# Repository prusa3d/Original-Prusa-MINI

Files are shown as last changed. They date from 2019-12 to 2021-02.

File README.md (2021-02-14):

# Original Prusa MINI / MINI+

The Original Prusa MINI / MINI+ is a 3D printer project maintained by PRUSA RESEARCH. Originates in the RepRap project.

This repository contains resources and documentation for printed and mechanical parts of the printer.

**Links**

 * Prusa Research website : http://prusa3d.com
 * Product page: https://www.prusa3d.com/original-prusa-mini/
 * Build manual: https://help.prusa3d.com/en/tag/mini-2/

 * Buddy-board : https://github.com/prusa3d/Buddy-board-MINI-PCB
 * Heatbed : https://github.com/prusa3d/Heatbed-Mini-PCB
 * IR senzor : https://github.com/prusa3d/MKxS-IR-sensor

<p align="center">
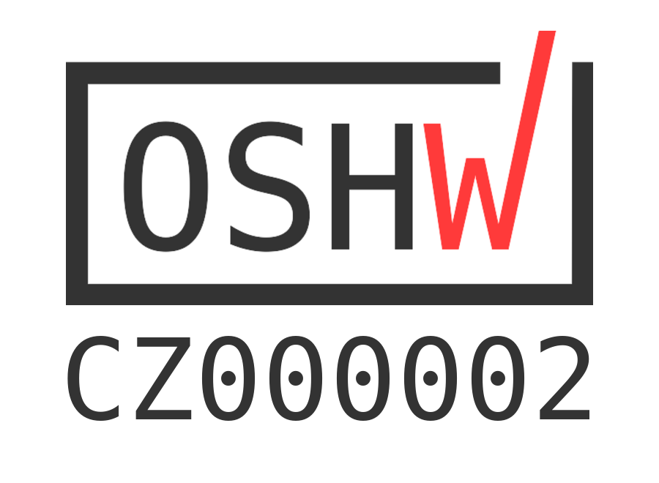
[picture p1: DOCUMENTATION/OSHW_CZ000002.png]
OSHW logo
  
</p>

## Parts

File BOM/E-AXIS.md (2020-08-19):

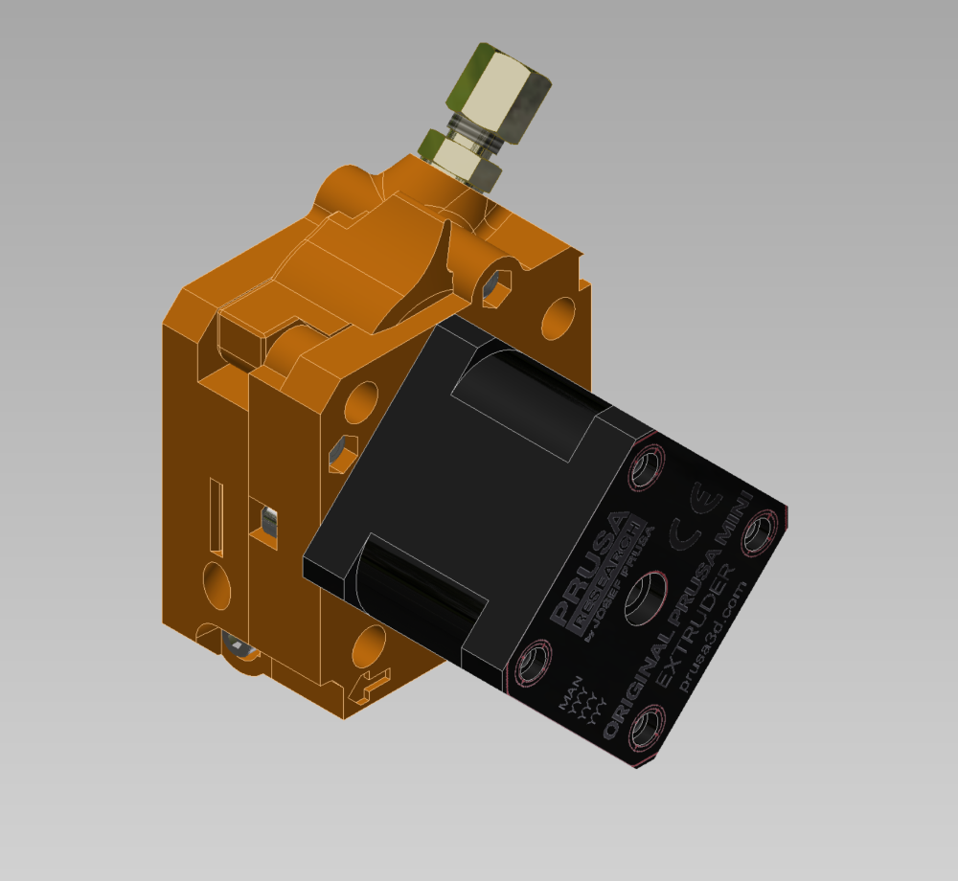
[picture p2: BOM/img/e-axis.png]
e-axis


**PRINTED PARTS**

|Name|Qty|
|:---|:---:|
|MINI-extruder-front|1|
|MINI-extruder-idler|1|
|MINI-extruder-rear|1|
|MINI-inspection-door|1|

**FASTENERS**

|Name|Qty|
|:---|:---:|
|M3x12 screw|3|
|M3x25 screw|6|
|M3x40 screw|1|
|M3n|4|
|M3nN|1|
|M3nS|1|

**ELECTRICAL PARTS**

|Name|Qty|
|:---|:---:|
|[MINI-E-axis motor](/DOCUMENTATION/ELECTRONICS/mini-motor-kit.pdf)|1|

**STANDARD PARTS**

|Name|Qty|
|:---|:---:|
|Bearing 625 2Z|2|
|MINI extruder idler spring|1|
|Zip tie|3|

**CUSTOM PARTS**

|Name|Qty|
|:---|:---:|
|[MINI fitting](/DOCUMENTATION/MECHANICAL%20PARTS/mini-fitting.pdf)|1|
|[MINI fitting swivel nut](/DOCUMENTATION/MECHANICAL%20PARTS/mini-fitting-swivel-nut.pdf)|1|
|[MINI fitting olive](/DOCUMENTATION/MECHANICAL%20PARTS/mini-fitting-olive.pdf)|1|
|[MINI motor pinion](/DOCUMENTATION/MECHANICAL%20PARTS/mini-motor-pinion.pdf)|1|
|[MINI filament spur](/DOCUMENTATION/MECHANICAL%20PARTS/mini-extruder-spur.pdf)|1|
|[MINI extruder PTFE tube 4x2x15](/DOCUMENTATION/MECHANICAL%20PARTS/PTFE-tube-extruder-15.pdf)|1|
|[MINI input PTFE tube 4x2x150](/DOCUMENTATION/MECHANICAL%20PARTS/PTFE-tube-input-150.pdf)|1|
|[MINI bowden 4x2x275](/DOCUMENTATION/MECHANICAL%20PARTS/PTFE-tube-bowden-275.pdf)|1|
|[MINI shaft 5x12](/DOCUMENTATION/MECHANICAL%20PARTS/mini-idler-shaft.pdf)|1|

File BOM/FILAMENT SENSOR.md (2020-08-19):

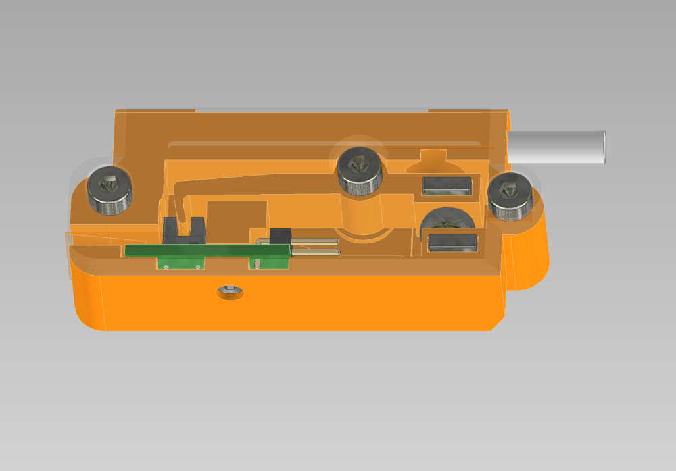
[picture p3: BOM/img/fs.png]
fs


**PRINTED PARTS**

|Name|Qty|
|:---|:---:|
|MINI-Fsensor-box|1|
|MINI-Fsensor-cover|1|
|MINI-Fsensor-lever|1|

**FASTENERS**

|Name|Qty|
|:---|:---:|
|M3x12 screw|4|
|M2x8 screw|1|

**ELECTRICAL PARTS**

|Name|Qty|
|:---|:---:|
|[IR filament sensor](https://github.com/prusa3d/MKxS-IR-sensor)|1|
|[IR filament sensor cable](/DOCUMENTATION/ELECTRONICS/mini-filament-sensor-cable.pdf)|1|

**STANDARD PARTS**

|Name|Qty|
|:---|:---:|
|Magnet 10x6x2|2|
|Stainless steel ball 7mm|1|

**CUSTOM PARTS**

|Name|Qty|
|:---|:---:|
|[MINI FS textile sleeve](/DOCUMENTATION/MECHANICAL%20PARTS/mini-oplet-5x300.pdf)|1|
|[MINI FS PTFE 4x2x15](/DOCUMENTATION/MECHANICAL%20PARTS/PTFE-tube-extruder-15.pdf)|1|

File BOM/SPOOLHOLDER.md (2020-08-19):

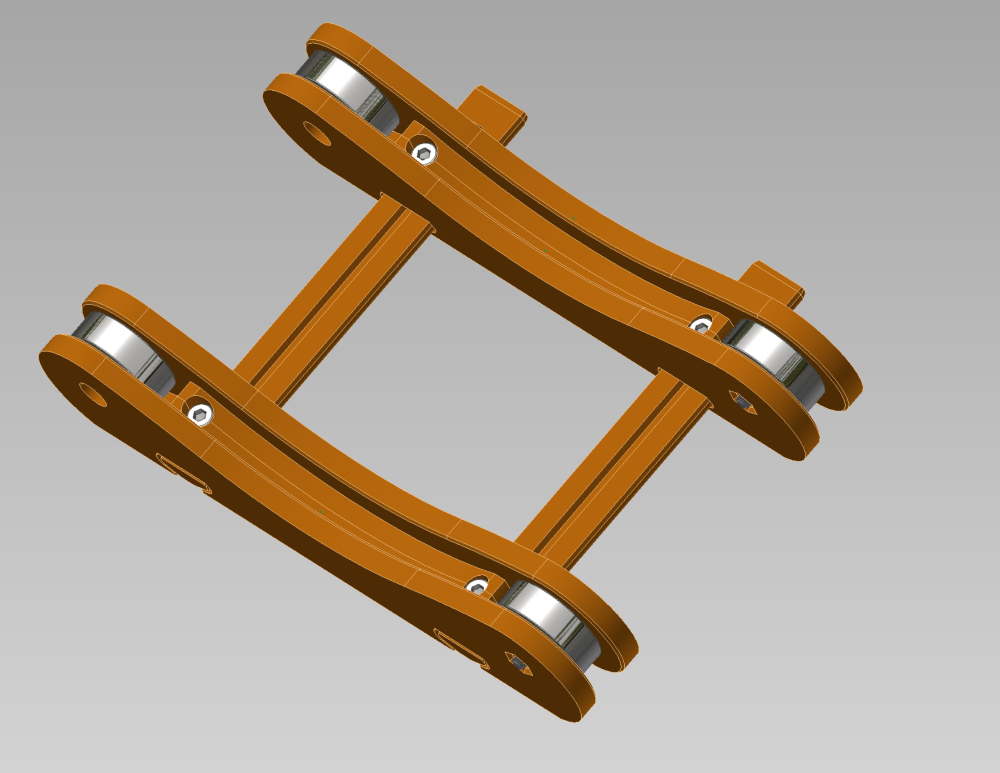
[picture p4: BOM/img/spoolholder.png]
spoolholder


**PRINTED PARTS**

|Name|Qty|
|:---|:---:|
|MINI-spoolholder-base|4|
|MINI-spoolholder-rail|2|

**FASTENERS**

|Name|Qty|
|:---|:---:|
|M3x8 screw|4|
|M3x12 screw|4|
|M3n|4|
		
**STANDARD PARTS**

|Name|Qty|
|:---|:---:|
|Bearing 608 2Z|4|

**CUSTOM PARTS**

|Name|Qty|
|:---|:---:|
|[MINI spoolholder foam pads](/DOCUMENTATION/MECHANICAL%20PARTS/mini-s-holder-pads.pdf)|4|

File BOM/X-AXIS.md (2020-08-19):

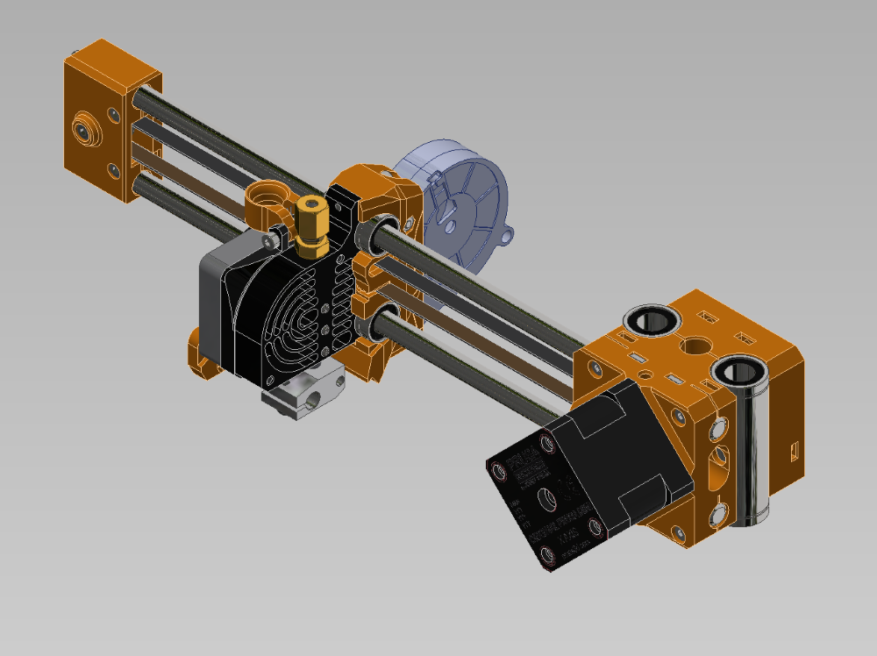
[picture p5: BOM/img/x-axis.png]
x-axis


**PRINTED PARTS**		

|Name|Qty|
|:---|:---:|
|MINI-x-carriage|1|
|MINI-x-end|1|
|MINI-z-carriage-front|1|
|MINI-z-carriage-rear|1|
|MINI-fan-spacer|1|
|MINI-fan-spacer-clip|1|
|MINI-minda-holder|1|

**FASTENERS**

|Name|Qty|
|:---|:---:|
|M3x12 screw|12|
|M3x20 screw|9|
|M3x30 screw|4|
|M3x10 button head screw|1|
|M3x4 grub screw|4|
|M3n|4|
|M3nN|1|
|M3nS|13|

**ELECTRICAL PARTS**

|Name|Qty|
|:---|:---:|
|[MINI hotend thermistor](/DOCUMENTATION/ELECTRONICS/mini-termistor.pdf)|1|
|[MINI heater](/DOCUMENTATION/ELECTRONICS/mini-heater.pdf)|1|
|[MINI heatsink fan](/DOCUMENTATION/ELECTRONICS/mini-extruder-fan.pdf)  ([DS](/DOCUMENTATION/ELECTRONICS/mini-extruder-fan-DS.pdf))|1|
|[MINI print fan](/DOCUMENTATION/ELECTRONICS/mini-turbine-fan.pdf)  ([DS](/DOCUMENTATION/ELECTRONICS/mini-turbine-fan-DS.pdf))|1|
|[MINI M.I.N.D.A.](/DOCUMENTATION/ELECTRONICS/mini-minda.pdf)|1|
|[2S connector](/DOCUMENTATION/ELECTRONICS/mini-2s.pdf)|1|
|[MINI X-axis motor](/DOCUMENTATION/ELECTRONICS/mini-motor-kit.pdf)|1|

**STANDARD PARTS**

|Name|Qty|
|:---|:---:|
|LM8UU linear bearing	|2|
|LM10LUU linear bearing|2|
|Pulley Bearing Idler 623h|1|
|Pulley Motor GT2-16|1|
|X-axis belt 561 mm|1|

**CUSTOM PARTS**

|Name|Qty|
|:---|:---:|
|[MINI X smooth rod](/DOCUMENTATION/MECHANICAL%20PARTS/mini-x-rod.pdf)|2|
|[MINI heatsink](/DOCUMENTATION/MECHANICAL%20PARTS/mini-heatsink.pdf)|1|
|[MINI heatbreak](/DOCUMENTATION/MECHANICAL%20PARTS/mini-heatbreak.pdf)|1|
|[MINI heaterblock](/DOCUMENTATION/MECHANICAL%20PARTS/mini-heaterblock.pdf)|1|
|[MINI nozzle 0.4](/DOCUMENTATION/MECHANICAL%20PARTS/mini-nozzle.pdf)|1|
|[MINI fitting](/DOCUMENTATION/MECHANICAL%20PARTS/mini-fitting.pdf)|1|
|[MINI fitting swivel nut](/DOCUMENTATION/MECHANICAL%20PARTS/mini-fitting-swivel-nut.pdf)|1|
|[MINI fitting olive](/DOCUMENTATION/MECHANICAL%20PARTS/mini-fitting-olive.pdf)|1|
|[MINI hotend PTFE tube 4x2x43.4](/DOCUMENTATION/MECHANICAL%20PARTS/PTFE-tube-hotend.pdf)|1|
|[MINI X motor textile sleeve](/DOCUMENTATION/MECHANICAL%20PARTS/mini-oplet-5x300.pdf)|1|
|[MINI hotend textile sleeve](/DOCUMENTATION/MECHANICAL%20PARTS/mini-oplet-8x700.pdf)|1|

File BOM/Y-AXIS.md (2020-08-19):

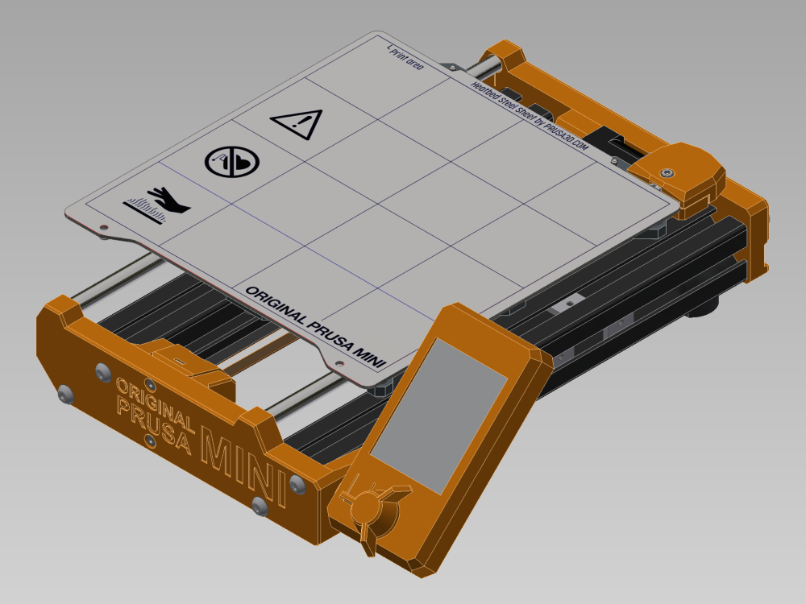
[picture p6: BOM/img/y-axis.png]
y-axis


**PRINTED PARTS**

|Name|Qty|
|:---|:---:|
|MINI-y-belt-holder|1|		
|MINI-y-idler|1|
|MINI-y-plate-front|1|	
|MINI-y-plate-rear|1|		
|MINI-heatbed-cable-cover-bottom|1|
|MINI-heatbed-cable-cover-top|1|		
|MINI-display-box|1|		
|MINI-knob|1|		

**FASTENERS**

|Name|Qty|
|:---|:---:|
|M3x8 screw|15|		
|M3x12 screw|7|		
|M3x20 screw|3|		
|M5x20r screw|8|		
|M3x4 Torx|9|		
|M3nN|11|		
|M3nS|2|		
|M3nE|3|		
|[M3x6 hex spacer](/DOCUMENTATION/MECHANICAL%20PARTS/mini-column.pdf)|9|		

**ELECTRICAL PARTS**

|Name|Qty|
|:---|:---:|
|[MINI heatbed](https://github.com/prusa3d/Heatbed-Mini-PCB)|1|		
|[MINI heatbed termistor](/DOCUMENTATION/ELECTRONICS/MK3s-HB-termistor.pdf)|1|		
|[MINI heatbed cable](/DOCUMENTATION/ELECTRONICS/mini-bed.pdf)|1|		
|[MINI Y-axis motor](/DOCUMENTATION/ELECTRONICS/mini-motor-kit.pdf)|1|		
|[MINI display](/DOCUMENTATION/ELECTRONICS/mini-display-ldopr28lcd-a003.zip)  [(driver DS)](/DOCUMENTATION/ELECTRONICS/mini-lcd-driver-st7789v.pdf)  [(lcd module DS)](/DOCUMENTATION/ELECTRONICS/mini-lcd-module-fw024tft-v14.pdf)|1|		
|[MINI lcd cable](/DOCUMENTATION/ELECTRONICS/mini-lcd-cable.pdf)|1|		

**STANDARD PARTS**

|Name|Qty|
|:---|:---:|
|LM8UU linear bearing|3|		
|Pulley Bearing Idler 623h|1|		
|Pulley Motor GT2-16|1|		
|Y-axis belt 496 mm|1|		 

**CUSTOM PARTS**

|Name|Qty|
|:---|:---:|
|[MINI aluminium extrusion 262mm](/DOCUMENTATION/MECHANICAL%20PARTS/mini-y-extrusion.pdf)|2|	
|[MINI Y smooth rod](/DOCUMENTATION/MECHANICAL%20PARTS/mini-y-rod.pdf)|2|		
|[MINI Y carriage](/DOCUMENTATION/MECHANICAL%20PARTS/mini-y-carriage.pdf)|1|		
|[MINI heatbed textile sleeve](/DOCUMENTATION/MECHANICAL%20PARTS/mini-oplet-5x350.pdf)|1|		
|[U bolt](/DOCUMENTATION/MECHANICAL%20PARTS/u-bolt.pdf)|3|		
|[MINI steel sheet](/DOCUMENTATION/MECHANICAL%20PARTS/mini-steelsheet-std.pdf)|1|		
|[MINI foam pad](/DOCUMENTATION/MECHANICAL%20PARTS/mini-foam-pad.pdf)|5|

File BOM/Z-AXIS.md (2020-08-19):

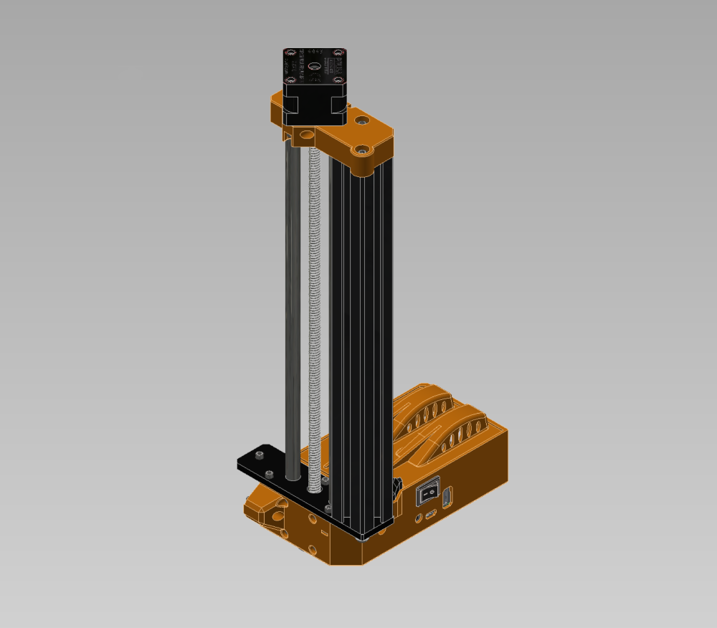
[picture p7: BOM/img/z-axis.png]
z-axis


**PRINTED PARTS**

|Name|Qty|
|:---|:---:|
|MINI-z-bottom|1|
|MINI-z-bottom-cover|1|
|MINI-z-bottom-cable-cover|1|
|MINI-z-top|1|

**FASTENERS**

|Name|Qty|
|:---|:---:|
|M3x8 screw|4|
|M3x12 screw|4|
|M3x20 screw|10|
|M3x40 screw|1|
|M5x16r screw|4|
|M3n|4|
|M3nS|10|

**ELECTRICAL PARTS**

|Name|Qty|
|:---|:---:|
|[MINI Buddy board v1.0.x](https://github.com/prusa3d/Buddy-board-MINI-PCB)|1|
|[MINI power switch](/DOCUMENTATION/ELECTRONICS/mini-power-switch.pdf)|1|
|[MINI display cable](/DOCUMENTATION/ELECTRONICS/mini-lcd-cable.pdf)|1|
|[MINI Z-axis motor](/DOCUMENTATION/ELECTRONICS/mini-motor-kit.pdf)|1|

**CUSTOM PARTS**		

|Name|Qty|
|:---|:---:|
|[MINI Z plate bottom](/DOCUMENTATION/MECHANICAL%20PARTS/mini-z-plate-bottom.pdf)|1|
|[MINI aluminium extrusion 289mm](/DOCUMENTATION/MECHANICAL%20PARTS/mini-z-extrusion.pdf)|1|
|[MINI Z smooth rod](/DOCUMENTATION/MECHANICAL%20PARTS/mini-z-rod.pdf)|2|

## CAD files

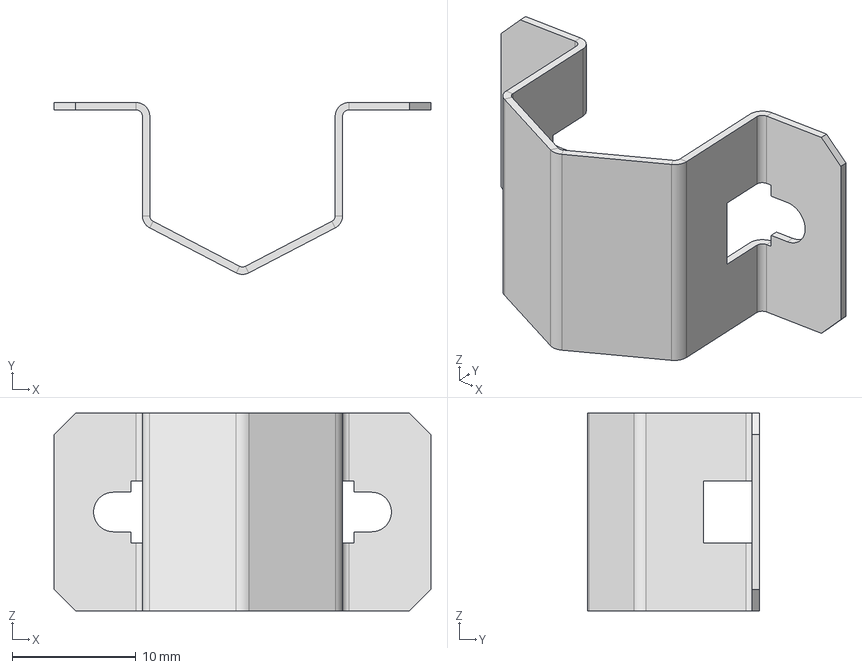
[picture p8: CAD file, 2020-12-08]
STEP/MECHANICAL PARTS/MINI-bearing-clip.stp
30.5 x 13.9 x 16.0 mm

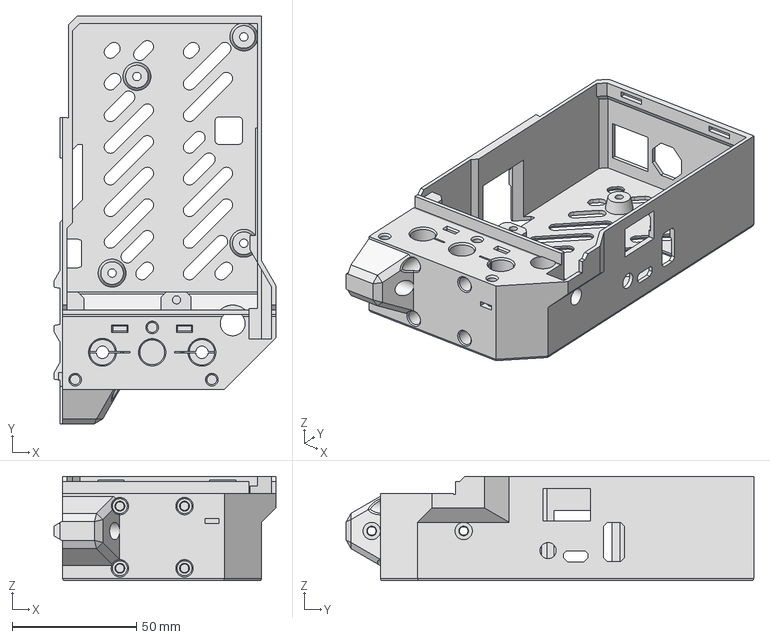
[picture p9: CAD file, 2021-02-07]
STEP/PRINTED PARTS/MINI-z-bottom.stp
89.3 x 163.9 x 42.0 mm

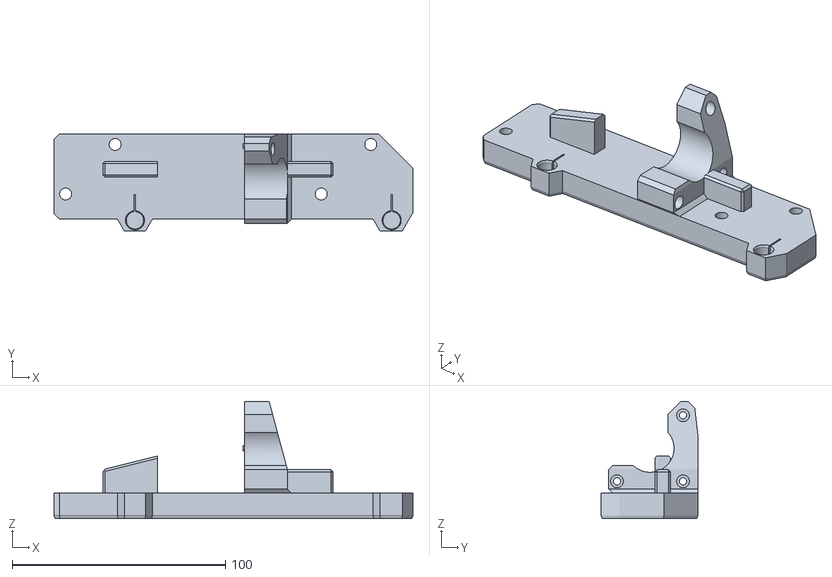
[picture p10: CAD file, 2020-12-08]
STL/MINI-y-plate-rear.stl
168.5 x 45.5 x 54.9

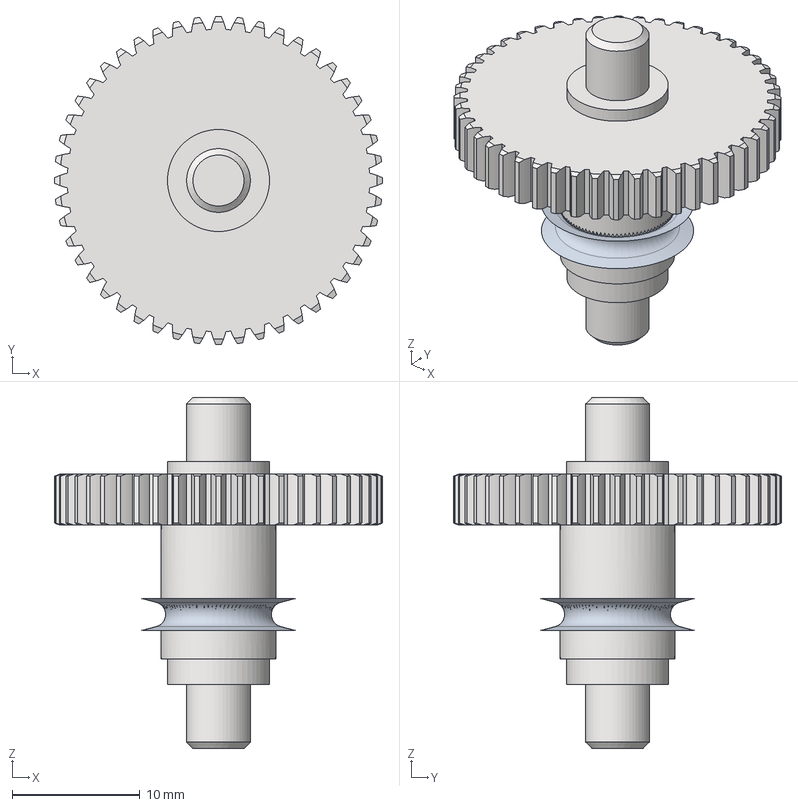
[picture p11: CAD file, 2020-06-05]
STEP/MECHANICAL PARTS/MINI-filament-spur.stp
25.7 x 25.7 x 27.5 mm

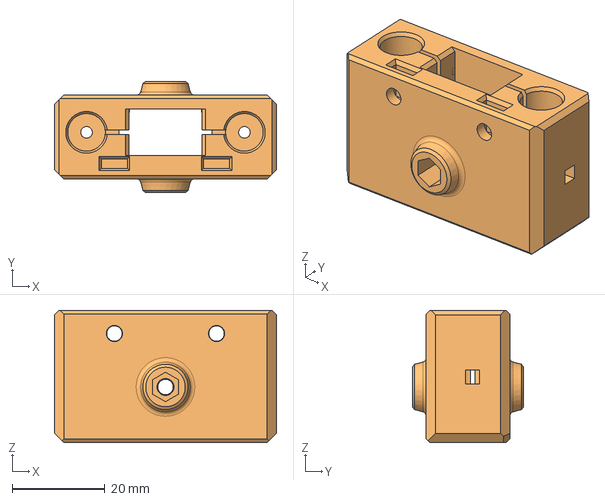
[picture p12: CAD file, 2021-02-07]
STEP/PRINTED PARTS/MINI-x-end.stp
47.8 x 24.0 x 28.5 mm

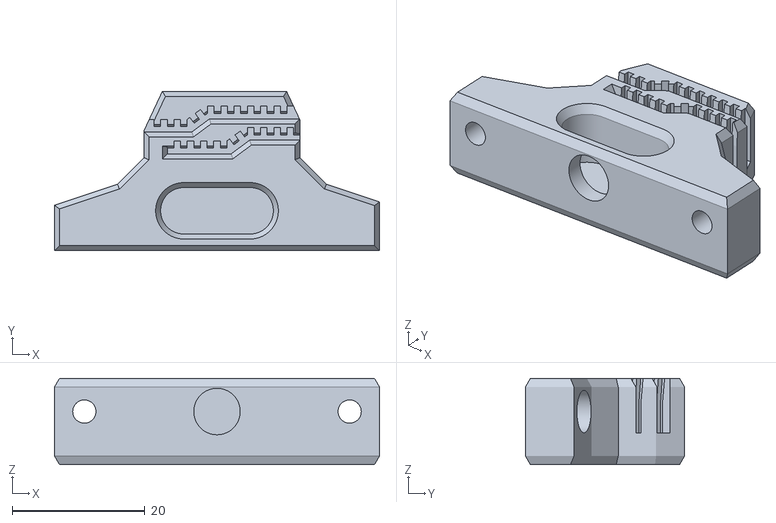
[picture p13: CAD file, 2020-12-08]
STL/MINI-y-belt-holder.stl
49.0 x 24.0 x 13.0

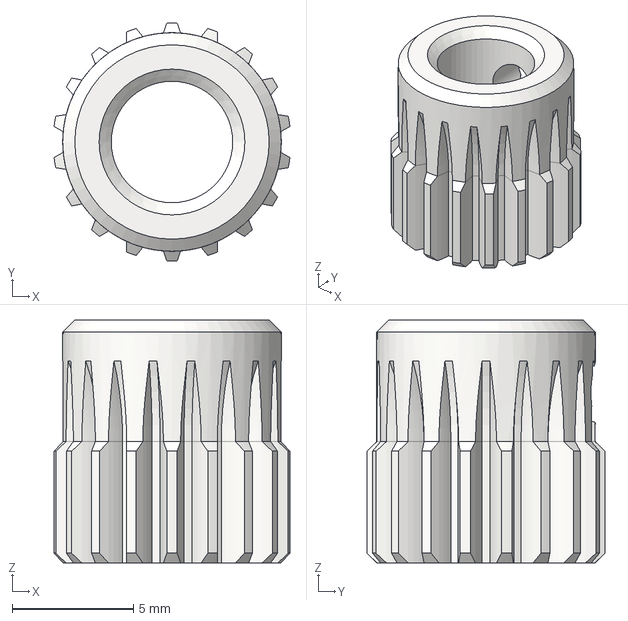
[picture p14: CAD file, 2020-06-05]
STEP/MECHANICAL PARTS/MINI-pinion.stp
9.72 x 9.80 x 10.0 mm

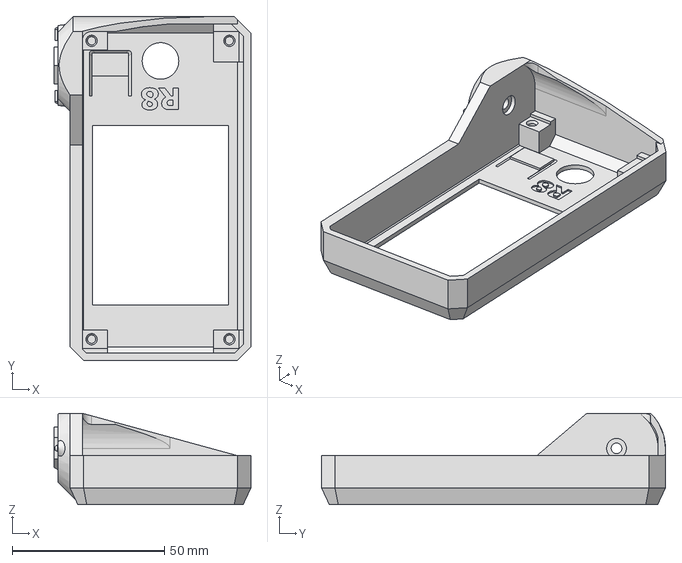
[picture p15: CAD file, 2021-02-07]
STEP/PRINTED PARTS/MINI-display-box.stp
64.6 x 112.9 x 30.0 mm

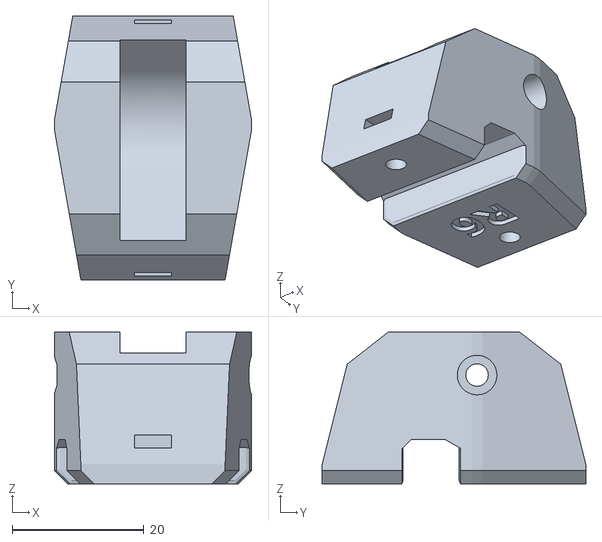
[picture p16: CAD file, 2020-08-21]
STL/MINI-y-idler.stl
29.9 x 40.0 x 23.0

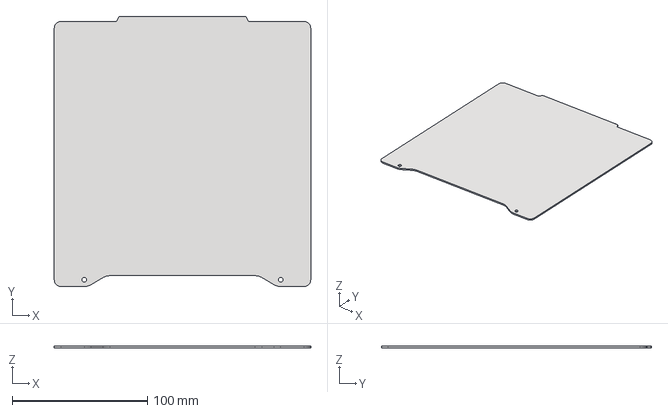
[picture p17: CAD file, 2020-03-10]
STEP/MECHANICAL PARTS/MINI-steel-sheet.stp
190.0 x 200.0 x 1.40 mm

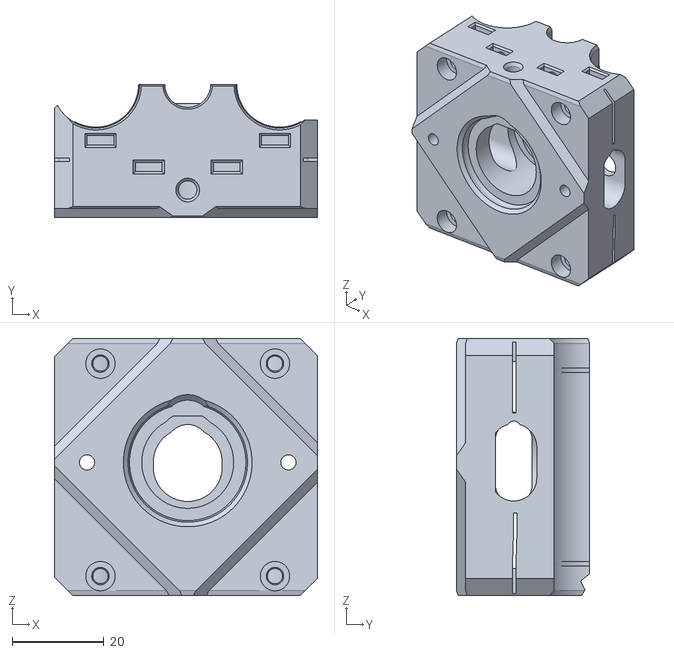
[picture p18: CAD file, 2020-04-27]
STL/MINI-z-carriage-front.stl
57.2 x 29.0 x 56.0

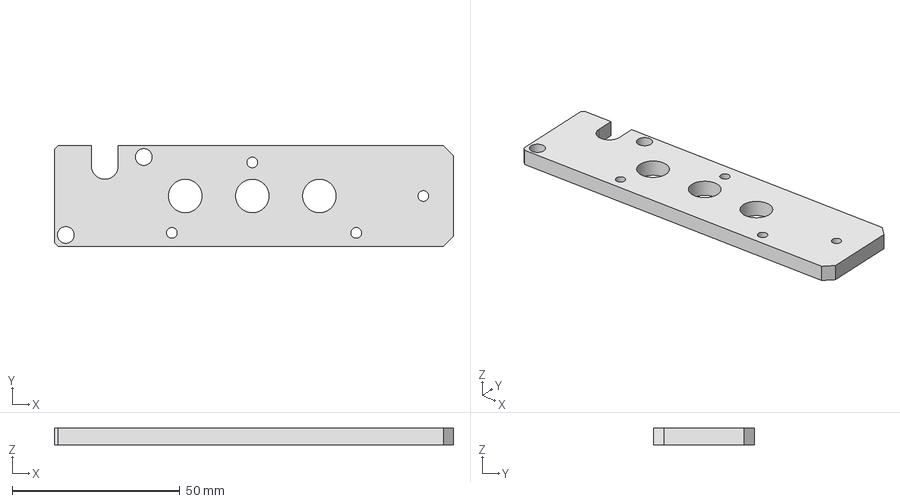
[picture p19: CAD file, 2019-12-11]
STEP/MECHANICAL PARTS/MINI-z-plate-bottom.stp
119.0 x 30.0 x 5.00 mm

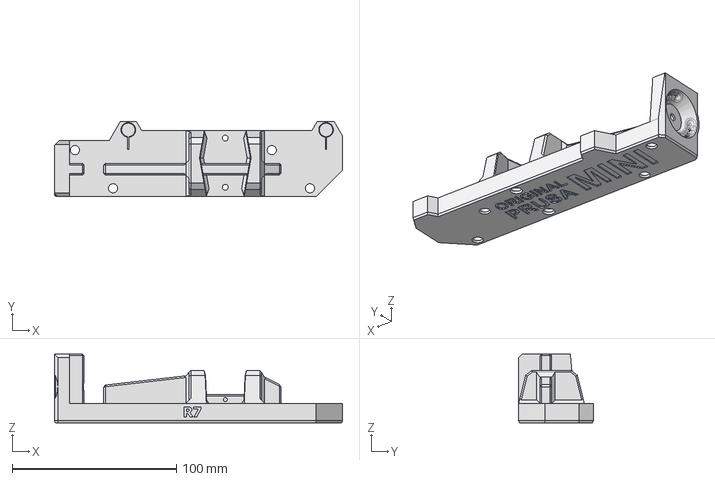
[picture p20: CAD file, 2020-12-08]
STEP/PRINTED PARTS/MINI-y-plate-front.stp
175.5 x 45.5 x 42.0 mm

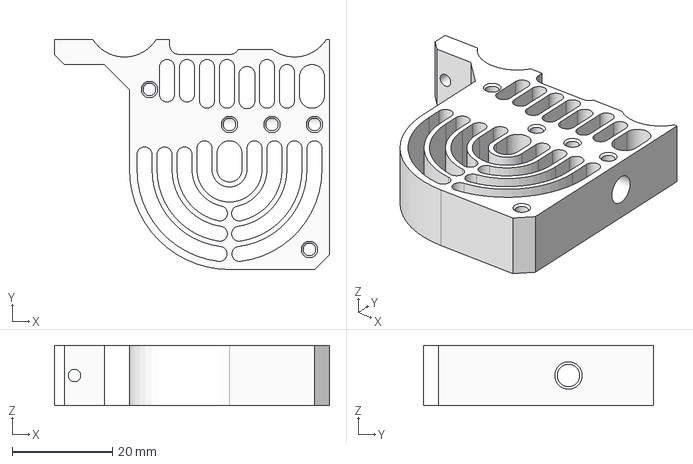
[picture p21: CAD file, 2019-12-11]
STEP/MECHANICAL PARTS/MINI-heatsink.stp
55.0 x 46.0 x 12.0 mm

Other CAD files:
STEP/PRINTED PARTS/MINI-y-plate-rear.stp
STL/MINI-z-bottom.stl
STEP/PRINTED PARTS/MINI-y-belt-holder.stp
STL/MINI-extruder-rear.stl
SOURCE/MECHANICAL PARTS/MINI-bearing-clip.ipt
SOURCE/MECHANICAL PARTS/MINI-filament-spur.ipt
SOURCE/MECHANICAL PARTS/MINI-heatbreak.ipt
SOURCE/MECHANICAL PARTS/MINI-heaterblock.ipt
SOURCE/MECHANICAL PARTS/MINI-heatsink.ipt
SOURCE/MECHANICAL PARTS/MINI-male-threaded-fitting.ipt
SOURCE/MECHANICAL PARTS/MINI-nozzle-0.4.ipt
SOURCE/MECHANICAL PARTS/MINI-olive.ipt
SOURCE/MECHANICAL PARTS/MINI-pinion.ipt
SOURCE/MECHANICAL PARTS/MINI-steel-sheet.ipt
SOURCE/MECHANICAL PARTS/MINI-swivel-nut.ipt
SOURCE/MECHANICAL PARTS/MINI-y-extrusion.ipt
SOURCE/MECHANICAL PARTS/MINI-z-extrusion.ipt
SOURCE/MECHANICAL PARTS/MINI-z-plate-bottom.ipt
SOURCE/PRINTED PARTS/MINI-base-spoolholder.ipt
SOURCE/PRINTED PARTS/MINI-display-box.ipt
SOURCE/PRINTED PARTS/MINI-extruder-front.ipt
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

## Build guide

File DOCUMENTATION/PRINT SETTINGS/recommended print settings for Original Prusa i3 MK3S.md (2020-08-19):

### Recommended print settings :

Printer : **Original Prusa i3 MK3S**

Print settings : **0.20mm Quality**

Material : **Prusament PETG**

Nozzle : **0.4 mm**

Layer : **0.2 mm**

Support : **no supports**

### **Edit :**

Infill pattern : **grid**

Infill density : **10 %**

<br/>

### **Parts :**

- MINI-z-bottom-cover

- MINI-z-bottom-cable-cover

- MINI-fan-spacer

- MINI-fan-spacer-clip

- MINI-fsenzor-box

- MINI-fsenzor-cover

- MINI-fsenzor-lever

- MINI-minda-holder

- MINI-inspection-door

- MINI-knob

- MINI-heatbed-cable-cover-bottom

- MINI-heatbed-cable-cover-top

- MINI-rail-spoolholder

- MINI-base-spoolholder

-------------------------------------------------------------------------------------------------------------------

### Recommended print settings :

Printer : **Original Prusa i3 MK3S**

Print settings : **0.20mm Quality**

Material : **Prusament PETG**

Nozzle : **0.4 mm**

Layer : **0.2 mm**

Support : **no supports**

### **Edit :**

Infill pattern : **grid**

Infill density : **20 %**

<br/>

### **Parts :**

- MINI-x-carriage

- MINI-x-end

- MINI-y-belt-holder

- MINI-y-idler

- MINI-y-plate-rear

- MINI-y-plate-front

- MINI-z-carriage-rear

- MINI-z-carriage-front

- MINI-z-bottom

- MINI-z-top

- MINI-extruder-rear

- MINI-extruder-front

- MINI-extruder-idler

- MINI-display-box

-----------------------------------------------------------------------------------------------

Please keep in mind thermal expansion of used material especially in XY plane. Printed parts are tempered by heatbed - then cooled down to room temperature so parts shrink.

```
Apply this linear relation: delta D´ = D * gamma * delta T
	delta D´	= final dimension difference
	D		= original dimension
	gamma		= coefficient of thermal expansion for used material
	delta T		= printed part temperature difference between current temperature 
			  while it's printed and ambient temperature in use

Example:
material	PETG: 	HB temp. = 90 [°C]
			amb. temp. = 25 [°C] 
delta T		90 - 25 = 65 [°C]
gamma		0.000068 [m/m*°C] [1/°C] (doesn't matter if Celsius or Kelvin)
D		100 [mm]
Use basic unit!

delta D´ = D * gamma * delta T
delta D´ = 0.1 * 0.000068 * 65
delta D´ = 0.000442 [m] = 0.442 [mm]
```

Linear thermal expansion works for each layer if there's any delta T but every layer has different delta T if the heatbed temperates printed part - the higher layer position the smaller delta T. It's due to cooling printed part by ambient air and air flow from print fan.

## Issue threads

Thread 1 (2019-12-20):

M600 / Filament change

Kasperc88, 2019-12-20:
There is two issues with the Original Prusa MINI and M600 (Filament change) that can be fixed with firmware.

Issues:

1#
When the printer unload the filament it will turn off the nozzle. This is fine. To load the new filament you have to press continue on the LCD,
and the printer will now heat up the nozzle to the target temperature. Once it hit the target temperature it will begin loading the filament.

This mean you have to sit and wait while you push the new filament into the tube so the printer can grab it. If it was not grabbet from the start
the filament will not be loaded correct and this lead to issue #2.

#2
After the printer thinks it have loaded the filament it will ask you if the color is correct. You can press "No" and it will extruder a small amount
of filament. But after this it will start to print. You do not get a new chance to say the color still isn't correct.

Fixes:
#1 - A option to tell the printer to begin loading the new filament
#2 - More chances to tell that the color isn't correct.

Bonus:
It could be helpfull if the z-axis raise alot more so we can clean the nozzle without burning our hands.

joeynuggetz, 2019-12-24:
Agree with the filament loading/unloading especially during a color change. Just got a ruined print because the filament didn't load on the first attempt (extruder gears didn't grab filament). Instead of asking if filament loaded just like any other printer it just assumed everything was fine when I said "no" to the color ok message. This needs to be fixed asap as color prints will fail if there are any problems encountered while loading new filament.

I do not have the filament sensor. Not sure if having one would have helped in this case.

charlesramsay, 2020-01-04:
I have found it impossible to unload PETG several times.  The unload routine does not allow the filament to be completely released.  I came up with a solution.  I cut the strand from the spool. Then I purge the remaining filament until it's beyond the stepper motor. Then I undo the bowden tube at the stepper. It works.

JohnnyDeer, 2020-06-15:
Hi @Kasperc88 , this issue is related to Prusa-Firmware-Buddy. Is duplicate of https://github.com/prusa3d/Prusa-Firmware-Buddy/issues/260 and https://github.com/prusa3d/Prusa-Firmware-Buddy/issues/361 so i´ll close this one. Thank you for suggestion and understanding.

Closed 2020-06-15.

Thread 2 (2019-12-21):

Not a firmware issue - MINDA height

AndyThirtover, 2019-12-21:
Dear Prusa

   My Mini was shipped with a lose MINDA.  It was not clear in the manual what the procedure for setting up the MINDA.  I got on to Tech Support and went with 1mm.

   So far my Mini does not have a perfect first layer for large prints - it is working though!

   I would like to be able to send jobs from my desk to the Mini which is in the basement.

   It would be useful to know progress of prints or be able to use OctoPrint.

   Overall, the finish is not quite as good as my 5000hr Mk3i3.

Regards

Andy

JohnnyDeer, 2020-06-15:
Hi @AndyThirtover , let me summarize your issue... first part with MINDA was solved with help of our Tech Support. Second part will be possible trough Prusa Connect in future. And you can use OctoPrint on MINI already.
First thing is about hardware and have been solved. Other suggestions are about firmware. So i´ll close this issue. You can crate feature request with your suggestion on Prusa-Firmware-Buddy. Thank you.

Closed 2020-06-15.

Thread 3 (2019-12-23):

STL and STEP Files don't open

6ffm70, 2019-12-23:
I'm having troubles opening the 3d files:
STL won't open in Prusaslicer; STEP won't open in two different professional CAD applications. I've also tried this on different computers to no avail.

Strankler, 2019-12-25:
same here.

6ffm70, 2019-12-30:
I've got this resolved:
I opened the downloaded files with an editor, and the first line showed the <html opening tag. Repeat for all tested files - positive.

I've downloaded the files with Chromium, using #RMB #Save link on the file link in the repo. Well, it's not the file that is linked, but another page.

Issue corrected by cloning the repo.

Closed 2019-12-30.

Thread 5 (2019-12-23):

Mesh Levelling has very weird behaviour

AndyThirtover, 2019-12-23:
4.0.1 Please view:

https://www.youtube.com/watch?v=rOWLI0K9chY

You'll see that the points 1-2 work perfectly and the 3-4-5 only go UP.  6-7-8 are ok and and that the MINDA does not operate.  Notice that 6-7-8 are ok and then 11-12 and 13 also go up (as do all of the points on the left hand side of the bed.

The net result is that this printer cannot be first layer calibrated.   It seems that the issue gets worse every time I power cycle/factory reset the printer.    I've managed one print on 4.0.0 but since the 4.0.1 upgrade this sad Prusa Mini has not managed a single print ;)

gregsaun, 2020-01-07:
@michalxfanta I suspect this is due to the too short cables on the hotend which wear the cables quicker than expected. I have made an improvement on your parts to help, you can find it here: https://www.thingiverse.com/thing:4065410

Is Prusa working on a solution for this issue? The best way I see today would be to provide a longer heater cartridge cable because this is the shortest and most problematic one.

JohnnyDeer, 2020-06-16:
Hi, this behavior is because cables of MINDA are broken. We sended replacements with new MINDA type and improved cable holder, wich solving this problems. If you still have this kind of MINDA issue please contact our Tech Support. Thank you.

Closed 2020-06-16.

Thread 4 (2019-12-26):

MINDA cable wire break (mesh bed leveling unexpected behaviour/does not proceed)

6ffm70, 2019-12-26:
**Description**: 4x4 point mesh bed leveling does not finish as expected. When process starts, MINDA light is off;
probing pos. 1 - the print head moves _up_ (couple of mm)
probing pos. 2 - the print head moves _up_ (couple of mm)
probing pos. 3 - MINDA light switches on, print head moves _down_, then up; here the process halts.

When moving the X-axis, the MINA light switches on in a position further away from the extruder; and switches off approximately at the same position when moving back into direction of the extruder.

This behaviour is reproduceable. With every go, the Z-Axis moves further up by a couple of mm.

**Analysis**: with the printer switched on, the MINDA light on or off, moving the MINA cable by hand makes the MINDA light flicker.

**Assumption**: at least one of the conductors in the MINDA cable is broken after ~30 hours of operation.

6ffm70, 2019-12-29:
**More Analysis**: locating the wire break in the cable
1. MINDA and cable in situ: removed textile sleeve, singled out MINDA cable
2. marking (I) the position of the top cable tie on the cable for reference (28.5cm from MINDA):
3. bending the cable starting at the sensor, moving in direction of connector end while watching the MINDA light
4. marking (II) the first position where the light flickers first (24cm from MINDA)
5. switching off printer, removing connector and cable
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
6. clean cutting cable on marking II in direction of MINDA
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
7. removing outer cable 15mm and wire isolation 7mm from cut of connector section half
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
8. measuring each resistance of all three wires while bending the cable in different sections: black OK, brown OK, blue NOK
9. locating the approximate point of non-contact in the blue wire by watching the multimeter and bending the cable, starting from the connector; marking (III) the approximate point (39cm from MINDA)
10. carefully stripping blue wire isolation from cut into direction of marking III
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
11. noting down position where stranded wire is separated (**29cm** (IV), **33.5cm** (V) from MINDA)
12. checking the remainder cable length for breaks with resistance measurement

6ffm70, 2019-12-29:
### There is no evidence for the root cause of the wire break so far. As long as the root cause is not eliminated, any replacement of the MINDA ass'y or repair hack is a temporary solution.

**Repair hack**:
Parts required: 5x cable ties 2.5mm, 4x wire end sleeves*, heat shrink hose ø3mm, ø6mm as required
Tools required: wire stripper 4mm², 0.25-0.4mm², copper wire shear, end sleeve crimp pliers (open type) 0.5mm²*
*alternatively a heat controlled soldering iron and soldering wire

1. clean cut off section with broken wire strands
2. stripping shortened blue wire for 7mm
3. preparing new isolated (yellow in pictures) wire in length of broken/removed wire with 7mm isolation stripped of both ends
4. crimping (to avoid uncontrolled heat) end of blue wire with one end of new wire with an end sleeve
5. isolating wire junction with heat shrink hose
6. removing outer cable 15mm and wire isolation 7mm from cut of MINDA section half
7. preparing 3x heat shrink hose over wire end, and 1x heat cable sleeve replacement shrink hose over cable in length of stripped section +30mm
8. repeat crimp connection for 3x wire connection
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
9. isolate 3x wire junction with heat shrink hoses
10. heat shrink cable sleeve replacement hose
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
11. place MINDA assembly back in printer using new cable ties
12. hope that changed internal wire resistances don't affect sensor operation

gregsaun, 2020-01-07:
The hotend cables on the Prusa Mini are very short and stressed which could potentially have damaged your wire quicker than expected.

I made a fix for those too short cables in case you want to solve it:
https://www.thingiverse.com/thing:4065410

6ffm70, 2020-01-14:
More follow up:

1. The cable as repaired above made the printer go again; however Mesh Bed Leveling gave different results by +/-0.400 each time, resulting in unsuccessful prints.
2. Replacing the repaired MINDA assembly with a new one provided by P/R support resolved this issue.
3. The cause of 1.) is unknown to me. Assumptions: one or both of the wires not repaired were damaged, and this was not detected during multimeter tests; or the repair affected sensor operation.

JohnnyDeer, 2020-06-16:
Hi @6ffm70 , we sended replacements with new MINDA type and improved cable holder, wich solving this problems. If you still have this kind of MINDA issue please contact our Tech Support. Thank you.

6ffm70, 2020-08-01:
Hello @JohnnyDeer, can you please elaborate on what is meant with _new MINDA type_? I've had a couple of MINDAs replaced by tech support, and they all showed similar symptoms, even with the improved cable holder.

6ffm70, 2020-08-26:
Follow up: new MINDA details added here: https://github.com/prusa3d/Original-Prusa-MINI/blob/master/DOCUMENTATION/ELECTRONICS/mini-minda.pdf

Closed 2020-06-16.

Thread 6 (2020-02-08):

MINI-y-plate-front.stl

VapeN3D, 2020-02-08:
Not able to download

JohnnyDeer, 2020-06-16:
Hi @VapeN3D , if you have issues with downloading on github, you can download file with all SLTs on our page ... https://www.prusa3d.com/prusa-i3-printable-parts/ . Same for your issue #17 . I´ll close both issues.

Closed 2020-06-16.

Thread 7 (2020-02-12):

Create high contrast large text size screen mode for people with limited vision

mrjohnc, 2020-02-12:
Create high contrast large text size screen mode for people with limited vision

This would include research on how to create accessibility modes for the screen by looking at guidelines and talking to groups of people with limited vision.

This mode may also include making additional sounds on certain actions to keep the user informed to what the printer is doing.

JohnnyDeer, 2020-06-15:
Hi @mrjohnc ,  this FR is related to firmware. Please create new one on Prusa-Firmware-Buddy following issue templates. I´ll close this one. Thank you for understanding.

Closed 2020-06-15.

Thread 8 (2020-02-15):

WiFi module support

rjkrause, 2020-02-15:
I have a question about the WiFi module.  In ESP 01 is the default FW or some modified version?  Or in the current version of FW in Buddy Board is still not supported WiFi ?

3d-gussner, 2020-04-06:
@rjkrause This question should be asked in https://github.com/prusa3d/Prusa-Firmware-Buddy.

Please close the issue.

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

JohnnyDeer, 2020-06-15:
Hi @rjkrause , this issue is related to firmware and is duplicate. I´ll close this one.

Closed 2020-06-15.

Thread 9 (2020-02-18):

Clicking Extruder gears

Superkirky, 2020-02-18:
Perhaps consider using helical gears for the extruder mechanism, to minimise backlash/noise. At the moment this is the most annoying/noisy part of the printer. Or perhaps stay with spur gear but include at spring loaded tensioning of the gear to reduce backlash/noise.

JohnnyDeer, 2020-06-22:
Hi @Superkirky , we know about this problematics, thank you for suggestion.

SnickCH, 2021-12-26:
How about using a dual gar extruder? maybe one like the extruder from the i3? Then you have a tested design that works

https://github.com/prusa3d/Original-Prusa-MINI/issues/58

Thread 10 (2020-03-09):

File names should scroll

hurley78, 2020-03-09:
File names should scroll because PrusaSlicer makes long file names and it makes it difficult to pick the file you want to print.  You can't see the filament type or print time.  Should scroll like MK3S.

3d-gussner, 2020-03-09:
@hurley78 This is a firmware issue you should post in https://github.com/prusa3d/Prusa-Firmware-Buddy

3d-gussner, 2020-04-06:
@hurley78 Can you please close the issue here?
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

Closed 2020-04-06.

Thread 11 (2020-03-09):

Stopping a print causes the printhead to crash into printed part.

HenrikPankoke, 2020-03-09:
I had a print with 6 elements printing individual.
The elements is place like the photo. print is from back left to back right.
moving to front left to front right
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

When printing the front right element I stopped the print.
the printhead then moves backwards an into the element behind. causing this to be knocked of the plate. In this case it was a small part and not theat high adhesion. But larger parts with could adhesion could have damage that fan on the printhead.
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

maybe changing stop command to move the nozzle up above highest printed element, before moving in any other direction. or just move nozzle clear of current print and stop movement.

HenrikPankoke, 2020-03-09:
Sorry. created this the wrong place. Don't know how to delete.
Moved to https://github.com/prusa3d/Prusa-Firmware-Buddy/issues/257

3d-gussner, 2020-04-06:
@HenrikPankoke you find a `Close issue` button below ;-)
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

JohnnyDeer, 2020-06-15:
I´m closing this issue as duplicate.

Closed 2020-06-15.

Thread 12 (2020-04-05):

feature request: support multiple steel sheets like the MK3

iandouglas, 2020-04-05:
Would be awesome if the Mini's firmware allowed us to switch more easily between the smooth PEI and the textured PEI like the MK3 firmware.

3d-gussner, 2020-04-06:
Hi @iandouglas,

you posted the issue in the wrong repository. Please close it here and open it in https://github.com/prusa3d/Prusa-Firmware-Buddy

iandouglas, 2020-04-07:
thanks again @3d-gussner

Closed 2020-04-07.

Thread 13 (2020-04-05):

feature request: holding in the knob to raise/lower Z like the MK3

iandouglas, 2020-04-05:
I miss being able to hold in the knob and adjusting the Z height when the printer is otherwise idle. Could this be added as a firmware feature in the future?

3d-gussner, 2020-04-06:
Hi @iandouglas,

you posted the issue in the wrong repository. Please close it here and open it in https://github.com/prusa3d/Prusa-Firmware-Buddy

iandouglas, 2020-04-07:
thanks @3d-gussner

3d-gussner, 2020-04-07:
@iandouglas You are welcome

Closed 2020-04-07.

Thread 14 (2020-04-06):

problem with ethernet mac adress

klimma1508, 2020-04-06:
Hello, I wanted to connect the 3D printer Prusa MINI via cable to the Internet, but the mac address of the 3d printer has only 11 characters, even if it has 12 characters. Does Prusa MINI support the internet or is it a mistake? Thank you Klimš
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

bobc, 2020-04-10:
There is a zero missing, i.e. use "0a" instead of "a" : 109C 700A FEFF

But you should really submit an issue in the Buddy firmware repo.

JohnnyDeer, 2020-06-15:
Hi @klimma1508 , this issue is related to firmware and have been already solved in version 4.0.5. I´ll close this issue.

Closed 2020-06-15.

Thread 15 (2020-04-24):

Prusa Mini Factory USB Stick failing

feutl, 2020-04-24:
Hello,

after some people do report the same problem on the Prusa Forum, I thought I should let you know.
The USB Stick shipped with the Prusa Mini fails after some time being mounted. I was happy the firmware update went through, but every print on the USB stick failed.

Copied the files to another USB stick and everything worked straight away.

https://forum.prusaprinters.org/forum/hardware-firmware-and-software-help/factory-usb-drive-wont-stay-mounted-on-printer-crashes-failed-prints/
https://forum.prusaprinters.org/forum/assembly-and-first-prints-troubleshooting/watchdog-reset-2/

3d-gussner, 2020-04-24:
Hi, I think you posted in wrong repository.

feutl, 2020-04-30:
>
>
> Hi, I think you posted in wrong repository.

which one would be the right repo ?
I experienced this with the Prusa MINI - and the forum seems not the right place at all

abosson, 2020-05-21:
I had the same problem with the USB stick... Dôme " watchdog reset" I change the USB stick and copy thé file without reslicing and I have no problem tête!

JohnnyDeer, 2020-06-15:
Hi @feutl , this issue is related to firmware and is duplicate of https://github.com/prusa3d/Prusa-Firmware-Buddy/issues/255 . I´ll close this one.

Closed 2020-06-15.

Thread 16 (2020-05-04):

Entering and exiting menu

geoper2, 2020-05-04:
When jumping from a submenu back to the main menu, for example from Filament back to Main, the highlight goes back to the first item which is Print.
The same happens when editing values inside a submenu. Upon exit the highlight goes to the first item on the submenu. This is furstrating because you need to scroll through all of the menu items to get back to the item you were before.

It would be better for the user experience to keep the highlight in the same place that you were before exit or back. When exiting or going back the highlight needs to remain in the same item and not move to the first item on the screen.

3d-gussner, 2020-05-04:
@geoper2 As you have a firmware issue post this here: https://github.com/prusa3d/Prusa-Firmware-Buddy
Please don't to forget to close this one.

Closed 2020-05-04.

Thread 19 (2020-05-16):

Solution to relieve stress on the hotend cables

martin8425, 2020-05-16:
In reference of: https://www.prusaprinters.org/prints/16515-prusa-mini-minda-saver-cable-guide

This is not my solution, but have been using it for some time. Merging this idea onto MINI-extruder-front.stl seams like a no-brainer to me ;)

JohnnyDeer, 2020-06-15:
Hi @martin8425 , thank you for your suggestion, we take note of this possibility.

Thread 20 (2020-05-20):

ABS as Filament Option missing

feutl, 2020-05-20:
The problem got raised in the forum
https://forum.prusaprinters.org/forum/hardware-firmware-and-software-help/abs-profile-on-mini

There is no "setting" for ABS as a filament to change, load or unload within the Prusa Mini firmware. This is a little confusing and the temperatures which should be used for ASA and ABS also seem to be different as I have understood.

Can this profile can be added somehow to the firmware?

Thanks

feutl, 2020-05-25:
https://github.com/prusa3d/Prusa-Firmware-Buddy/issues/493 posted it at the buddy-board repo

Closed 2020-05-25.

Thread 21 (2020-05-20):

OpenSCAD?

infosisio, 2020-05-20:
Is there a particular reason that this wasn't designed in OpenSCAD as per the usual tradition?

Thanks.

JohnnyDeer, 2020-06-15:
Hi @infosisio , reason why we are no longer using OpenSCAD is that we found better solution.

infosisio, 2020-06-15:
@JohnnyDeer I don't know what solution you found but you are no longer sharing them in a format the community can build upon.

JohnnyDeer, 2020-06-22:
@infosisio we are still sharing all data in format which is usable to build upon.

infosisio, 2020-06-22:
@JohnnyDeer That is not true, STEP is an archival format that doesn't give parametric control. The only thing it is useful for is to act as reference for reverse engineering a part, in order to be able to make changes and improvements. Please reconsider this.

SyberxSpace, 2020-06-22:
From the headers in the released STEP files it appears they were generated using Autodesk Inventor. Example from MINI-x-end.stp:
```
FILE_NAME(
/* name */
'MINI-x-end.stp',
/* time_stamp */ '2020-01-22T16:21:13+01:00',
/* author */ ('Robert Turinsky'),
/* organization */ (''),
/* preprocessor_version */ 'ST-DEVELOPER v17.2',
/* originating_system */ 'Autodesk Inventor 2019',
/* authorisation */ '');
```
I believe this would mean that the STEP files are indeed not the source files, and that this would make the printer not open-source as claimed. This also severely hampers the speed and accuracy of community improvements. Even if you Prusa Research believes that STEP files are source files **(please make clear if this is the case)**, I think it can be agreed that the practice is against the community accepted definition of the term and how it is used to imply an ecosystem encouraging communal improvement and iteration.

CacikeOtoao, 2020-06-22:
Sadly this has been happening more often that a lot of us would like. They have been dragging their feet to release source files or just setting their own timelines and borderline redefining the licenses used to release their products. They have actually made changes to some of the “Open Source” products and not update the git files until been pressed on. @JohnnyDeer  it is not about releasing “usable files to build upon”, it is about releasing the actual source files for products that are touted as Open Source and come with a big Open Source logo stamped on the box.

infosisio, 2020-06-24:
@JohnnyDeer I am sorry to say this but we are not talking to a wall here. You've heard our points clearly and you owe us a response. You market something as open source when it's not. Please explain yourselves.

CacikeOtoao, 2020-06-24:
I will also like an explanation, hopefully this is not a case of #openwashing.

lord-carlos, 2020-06-24:
It's a bit like releasing a binary Java file and calling it open source because you can decompile it.

It's nice that Prusa is releasing the step file, but calling it an open source printer at the same time is appalling.
On the shop site it even says:
> All parts of our printer are open-source.

infosisio, 2020-06-26:
@CacikeOtoao Unfortunately so far this seems to be the case...

josefprusa, 2020-06-30:
Let me clarify and correct some statements here from our side.
We have used openSCAD for long time, but from certain moment we needed to switch to more advanced sw for several reasons - starting from increasing speed of development, documentation, more advanced features available and ending up with easier exchange of data with our suppliers.
For GIT we choose STEP file format as this is widely used for exchange of data ( STEP = Standard for the Exchange of Product model data) and in fact it has been requested often by developers who did not like openSCAD in MK3 repository as alternative. Also, STEP files are widely accepted by various CAD software, it is standard how to exchange CAD information but   I do agree that STEP is not ideal for later development as you do loose some functionality or information as discussed here.
Starting with MINI repository we will add native source files in addition to STEP files ( we now use Autodesk Inventor ) and missing pieces of documentation in short time.

infosisio, 2020-06-30:
@josefprusa Thank you for agreeing to provide the source files but allow me to say as a response to your argument that STEP is not sufficient for an open source project, it is simply not the source file. Thanks.

SyberxSpace, 2020-07-01:
Thank you @josefprusa for agreeing that native source files are important for the community to develop and improve in an open and efficient manner. I'm hoping this will also carry over to the mk3s parts that also lack source files at the moment.

In the future you might want to consider a different license on release and make it clear what your release schedule and intents are from the beginning. "Surprises" like the appendix being released post-preorder and the lack of files and firmware tools aren't good for the community or how your brand is seen by the community. Not too long ago you were an outstanding example of what was good in the open community and these recent evens have begun to tarnish that. I don't think it's too late to turn that around though!

TLDR: The community is smart enough to understand if you just tell them what you plan outright. Just be **open** about it and stay faithful to the true intent of the open-source practice if you really want to be called open-source. Don't just do the minimum to keep the open tag on your products as it just makes you look untrustworthy.

I'm excited and hopeful for the future!

ucirello, 2021-02-23:
Prusa can keep the Autodesk Inventor files - as long as they release a version in openscad (or freecad for that matter) that the community can open and modify at source level, not at archive level (like Step or STL).

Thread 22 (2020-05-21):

Scrolling name of print for mini ?

abosson, 2020-05-21:
hello, I would suggest you  an improvement for the Mini !

the name of the print file is fixed and sometimes when you have to print the same part but with a différent material , the type of material is at the end of the name !

unfortunely, we can see it like on the MK3.

if it could be "scrolling" it could be great.

I don't if it's possible with the new mainboard but it would be useful in my case (when you have the listing)

JohnnyDeer, 2020-06-15:
Hi @abosson , this issue is related to Prusa-Firmware-Buddy and is duplicate of https://github.com/prusa3d/Prusa-Firmware-Buddy/issues/249 . I´ll close this one. Thank you for suggestion and understanding.

Closed 2020-06-15.

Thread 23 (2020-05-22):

Feature request: Loading filament improvement.

nigeljohnson73, 2020-05-22:
When you're loading, that step where it says click next to load, then gives you exactly zero seconds to ram filament in... well, it could turn the extruder stepper slowly to get the filament a catch, then clicking next would perform the load. That would be sooooo helpful.

JohnnyDeer, 2020-06-15:
Hi @nigeljohnson73 , this is also related to firmware and is similar to https://github.com/prusa3d/Prusa-Firmware-Buddy/issues/260 . I'll close this one.

Closed 2020-06-15.

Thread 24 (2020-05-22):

Feature request: loading filament - don't heat the bed

nigeljohnson73, 2020-05-22:
It's not required for the loading process, and it's wasteful.

JohnnyDeer, 2020-06-15:
Hi @nigeljohnson73 , this FR is related to firmware. Please create new one on Prusa-Firmware-Buddy following issue templates. I´ll close this one. Thank you for understanding.

Closed 2020-06-15.

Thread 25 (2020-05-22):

Feature request: loading filament - cooldown after load

nigeljohnson73, 2020-05-22:
You have to select a filament regardless of the current nozzle temp so it will heat up (even from cold), but you should also automatically cool down after the load as well... or remove the option to heat so that people know they have to to do it and stop the heating before walking away leaving the hot-end hot.

JohnnyDeer, 2020-06-15:
Hi @nigeljohnson73 , this issue is related to firmware and is duplicate of https://github.com/prusa3d/Prusa-Firmware-Buddy/issues/439 and https://github.com/prusa3d/Prusa-Firmware-Buddy/issues/221 . I'll close this one.

Closed 2020-06-15.

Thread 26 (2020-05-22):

Feature request: loading filament - use current temps

nigeljohnson73, 2020-05-22:
What if my particular filament isn't on the list??? allow for using the current temp, or remove the list... how is that list updated?

JohnnyDeer, 2020-06-15:
Hi @nigeljohnson73 , this FR is related to firmware. Please create new one on Prusa-Firmware-Buddy following issue templates. I´ll close this one. Thank you for understanding.

Closed 2020-06-15.

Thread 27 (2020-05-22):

Feature request: Show last M117 message

nigeljohnson73, 2020-05-22:
Yeah there is an option to look at all the messages, but it would be nice to see the last one on the screen somewhere just so you can watch the status as you run through your printer start code for example.

JohnnyDeer, 2020-06-15:
Hi @nigeljohnson73 , this FR is related to firmware. Please create new one on Prusa-Firmware-Buddy following issue templates. I´ll close this one. Thank you for understanding.

Closed 2020-06-15.

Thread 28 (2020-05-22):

Feature request: access the menus system while "Remote Printing"

nigeljohnson73, 2020-05-22:
I love the OctoPrint logo when it's connected, but you cannot access the menus so, for example, you cannot load filament. You need to power cycle the printer do the load, then go back to octoprint to reconnect.

JohnnyDeer, 2020-06-15:
Hi @nigeljohnson73 , this issue is related to firmware and is duplicate of https://github.com/prusa3d/Prusa-Firmware-Buddy/issues/360. I'll close this one.

Closed 2020-06-15.

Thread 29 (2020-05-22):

Bug: Disconnecting "Remote Printer" does not return control to the Mini

nigeljohnson73, 2020-05-22:
When you connect OctoPrint, you get the big logo. But, when you disconnect OctoPrint, the printer does not detect this and so you are forced to power cycle the printer to get control back. A workaround would be #28

Gordontgopher, 2020-06-06:
You've opened a number of issues in the hardware repository. The developers are more likely if you raiser them in the firmware repository (https://github.com/prusa3d/Prusa-Firmware-Buddy)

JohnnyDeer, 2020-06-15:
Hi @nigeljohnson73 , same as #28. I´m closing as duplicate.

Closed 2020-06-15.

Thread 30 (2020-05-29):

Spool holder

okaerin, 2020-05-29:
I want to print additional spool holder for my prusa mini. To do so I would need the required parts. Unfortunately I havent seen a part list. Is there one?

EuphoricPenguin, 2020-07-01:
https://trello.com/b/IHnQ677R/part-list-bom

pltaylor, 2021-05-27:
I know this is almost a year old, but I think this could be closed out now that the BOM is located here https://github.com/prusa3d/Original-Prusa-MINI/blob/master/BOM/SPOOLHOLDER.md

Closed 2021-05-27.

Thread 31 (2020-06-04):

Extruder Gears STEP files missing.

CacikeOtoao, 2020-06-04:
Hi,
The extruder for the MINI seems to be under the same license as the other components but the STEP files are not included. Is the extruder not Open Source? Any reason for the delay of the files been release?

akukan, 2020-06-05:
Missing parts have been uploaded, sorry for delay.

Closed 2020-06-05.

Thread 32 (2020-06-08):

Magnet Improvement Suggestion

Porch11, 2020-06-08:
I use the Prusa Mini almost daily. The steel plate installation and removal could be made easier if the magnets didn't pull it from a range/distance. I would suggest replacing them with Polymagnets; which are programmed permanent magnets that can be made from any magnet grade.

I believe they will give a better user experience, hold the plate better and be cheaper than the current system as it requires 12 magnets. I think with Polymagnets, you could get away easily with 8.

Here is a link to attachment Polymagnets: https://catalog.polymagnet.com/polymagnet-products/attach.html

JohnnyDeer, 2020-06-15:
Hi @Porch11 , thank you for your suggestion, we take note of this possibility.

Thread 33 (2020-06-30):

Multicolor print - unsuccessful load filament

Wolfram3D, 2020-06-30:
When print of first color is done there is color changing phase. When load of new filament/color is successful everything is ok but when load is not successful (eg extruder doesn't grab the filament) there is no chance to repeat load filament - just question if color is ok.

Is possible to improve it like:
1) print of first color
2) color change phase ->
   a) auto unload filament -> was filament successfully unloaded? When "Y" then press continue to load new filament. When "N" then repeat this step "unload filament".
   b) load filament -> was filament successfully loaded? When "Y" then purge and question if color is ok.... When "N" then repeat this step "filament loading".

Thanks

JohnnyDeer, 2020-07-07:
Hi @Wolfram3D , you are in bad section. Your issue is related to Buddy firmware and this issue is solved in FW version 4.1.0-RC1, i'm closing this one.

Closed 2020-07-07.

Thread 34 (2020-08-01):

Prusa Mini Open Source Design

6ffm70, 2020-08-01:
Seeing the good attitude towards open source hardware, software and mechanic design at Prusa Research marks a new era for me. An innovative, fast growing company that benefits from sharing, and lets others benefit from sharing:
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
Looking at the mechanic design in the repositories here, I have the impression that the open source design promise is not met, when I compare this to the creation of software: everything is available to modify, build and test it to a highly productive level.
External people, individuals and professional contribute, and have the opportunity to try new features.

Not so on the mechanic side - this is pretty much closed to Prusa internal and largely undocumented and incomplete. If traces are to be found, they are scattered over different sites in different categories. This is a missed opportunity to let P/R and the community benefit from open-source.

6ffm70, 2020-08-01:
To have this set up, I'd like to see

- 3d design definitions that can be modified. Unlike #21 , I don't think that has to be a particular file format like openSCAD. Inventor and STEP files should be okay, as people used different CAD systems to contribute. Though, if external references or skeleton models are used, this should stay intact within the native CAD files.
- Product and component specifications: the requirements for the entire product should be broken down to component level - including engineering drawings or model based definitions. Test cases and criteria, tolerances, tolerance calculations, and where applicable D-FMEA.
- If there are third party components that are not open source, they should include a datasheet and a customer volume model; if those parts are customer (Prusa) directed, like some E3D components on the Mk3, the specifications and all other open source data should be included too.
- Production data - the saying goes that Prusa printers can reproduce large parts of themselves (for all 3d-printed components), yet, there's only STL files in the repo, and no printing parameters. I'm with #18 here - why keep the -no doubt- super refined and experienced printing parameters P/R internal? The 3mf files, and the material properties should be open too.
- Everything in one place: an example: I only learned by chance that Mk3 and Mk3s use different PTFE tube diameters by tenths of a millimetre. That information was buried deep in support articles; even though it's relevant to function of the printer, and I was troubleshooting mine. I see that Github is more limited to version 3d designs while maintaining file relations, than a PDM system. Maybe enhance prusaprinters.org to host community design projects, and showcase this function by maintaining all engineering data for the printers there?
When this is properly set up, I'm sure external designer will branch out designs, test, enhance, etc. The current quality of sharing is discouraging this, to be honest.

gregsaun, 2020-08-01:
I think you made a good summary of the situation.

However, I am not okay with STEP file being a source. Even for designing a simple cube you have to start with a sketch and some defined dimensions and constraints (90° angle for example). If you export as STEP you loose this sketch and so part of the logic behind the design. Note that the dimensions and constraints are not the only logic you are loosing but also the sequence used to design a part. Some parts can be fairly complex to design and requires some special steps.

Just a side note regarding MK3(S) printers, they have never been sold as open source as far as I remember. Nothing was ever mentioned in this sense on the prusa3d.com pages nor in the launch video. It was just made well enough to think it is an open source printer but it is not. The Prusa Mini is different as it has been claimed in several places to be an open source printer and they even mention "All parts of our printer are open-source" (and not _all printed parts_).

6ffm70, 2020-08-01:
@gregsaun, this is grabbed from https://www.prusa3d.com/about-us/ , and this is what I also mean by good attitude towards open source hardware - it covers everything:
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
The fragments of the i3 Mk3/s design published in the github repo have the GPL licenece attached as well as the MINI.

I don't think the _sources_ of the mechanic design are deliberately incomplete. **Lack of an established method to collaborate in public may be a cause for this.**

This is also where STEP (subject to a lot of discussions eg. here https://github.com/prusa3d/Original-Prusa-i3/issues/139, https://github.com/prusa3d/Original-Prusa-i3/issues/84#) comes in as an _addition_ to the native format - it opens up editing access to the highest possible share of the community.

The tool of choice for the main branch will be set by the main developer; yesterday it was openSCAD, today it's Inventor (or some that identifies as Inventor), tomorrow it's another solution that fits the development requirements.

I think your concerns about the STEP format are valid; while at the same time my issue is the completeness of the _source_ of all mechanical engineering aspects of the printers.

Example: even if all native parametric 3d files were published online, you'd still only see how they were drawn/modelled, but not how the whole system works, or which design features or tolerances/materials have been chosen to overcome e.g. a heat dissipation challenge. You'd not be able to build on this knowledge to enhance this feature.

When calling the whole product, thus also the mechanical engineering _open source_, the community should be able to engineer the whole printer from scratch to make the project benefit from its contributions.

gregsaun, 2020-08-02:
@6ffm70 I agree for the STEP file, it is important to me to share them if you want to share properly your project. However they are not the source. You can create a STEP from the source but can't create the source from the STEP file. GPL is clear, you must share the source, it is not optional.

I agree with you that a CAD files alone isn't valid, you need to have the drawings for the tolerances/material/surface finish for "metal" parts and the print settings for the printed parts.

Good point regarding the about-us section. Then a lot more is missing like the specs of the fans, the specs of the extruder spring, the magnet specs, the whole BOM, etc. And this is valid for MK2(S) and MK2.5(S) as well (and probably MK1).

_> I don't think the sources of the mechanic design are deliberately incomplete. Lack of an established method for open collaboration may be a cause for this._
I think the community here starts to see this differently now. It is really not the first time we ask for the source files for MK2(S), MK2.5(S), MK3(S) and MINI. They had many many chances to fix this.

EuphoricPenguin, 2020-08-25:
I think the recent additions might push this thread closer to being closed, but there's still a distinct lack of community involvement on the hardware side; at least we have more or less complete documentation.

6ffm70, 2020-08-26:
@EuphoricPenguin , I agree, this is a leap forward!
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
JohnnyDeer, 2020-11-19:
Original Prusa MINI is now certified by Open Source HW Aliance - https://certification.oshwa.org/cz000002.html
I believe this issue can be closed as well as #21, @6ffm70 ?

lord-carlos, 2020-12-08:
> Original Prusa MINI is now certified by Open Source HW Aliance - https://certification.oshwa.org/cz000002.html
> I believe this issue can be closed as well as #21, @6ffm70 ?

That is only for software, no?
Hardware is "other"

ucirello, 2021-02-23:
By effectively forcing the use of a closed source software for the original design, this printer should not be labeled as open source hardware. Especially, because Autodesk Inventor is a very expensive software. By using an expensive proprietary software, Prusa is effectively locking contributions and fork out of this design.

6ffm70, 2021-03-02:
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

That's true - there is no licence for the hardware; and no licence for the documentation; just links to the github repo.
@JohnnyDeer can you please be more specific as to what has been certified?

bomarspub, 2021-03-17:
I found this to me an interesting read. I am currently reviewing the mechanicals, and several things are puzzling. I get it that its a volunteer effort, but maybe a little mechanical drafting guidance is in order. One thing is the absence of a preferred vendor part number is absent from the drawing.  Two  The mechanical call outs seem to be all over the map and need more explanation to the intention. Possibly a legend for international sharing to make more sense out of them. Cases where bubbles indicate there should be a second sheet or a defined note, yet absent. Just using the rods as a simple example, X rod is missing the rockwell spec.  Certainly can purchase this over the counter , but it would be nice to have a preferred vendor to work with. my two cents..

pltaylor, 2021-05-27:
> By effectively forcing the use of a closed source software for the original design, this printer should not be labeled as open source hardware. Especially, because Autodesk Inventor is a very expensive software. By using an expensive proprietary software, Prusa is effectively locking contributions and fork out of this design.

It may not be in the true spirit of open source, but asking Prusa to hamstring themselves by forcing the use of open source design tools may be a bridge too far.  At the end of the day Prusa is a business and they need to use the tools they think will help them get the job done.  Every step towards a pure open source is commendable, but like everything else in engineering there has to be a balance of multiple factors.

ucirello, 2021-05-27:
@pltaylor they can keep the originals in a closed format, and release the source in a open format that actually has the same object tree (freeCAD comes to mind, but not only). No need to hamstring themselves - but take the effort of saving into more (and open) formats.

pltaylor, 2021-05-27:
But if you submit a PR they would have to then do a manual merge into their preferred design software.  If the goal is to make modifications for yourself, then yes, your suggestion works.  But if the goal is to actually collaborate and grow the platform then your suggestion doesn't scale much better than the current state of things.

ucirello, 2021-05-27:
So just declare Mini to not be open source and be done with it.

6ffm70, 2021-05-29:
> But if you submit a PR they would have to then do a manual merge into their preferred design software. If the goal is to make modifications for yourself, then yes, your suggestion works. But if the goal is to actually collaborate and grow the platform then your suggestion doesn't scale much better than the current state of things.

I can see your point, and I believe it is a description of the ideal situation - which should certainly be the goal.
At the same time, the software available for collaborative mechanical design (PDM and CAD) is excellent for productivity and maintaining references, file associations and design intents; however none of these is open source.

This leaves the STEP format as the lowest common (open) exchange format, for the price of abandoning design parameters and intent, but maintaining accuracy. For now, the best every creator of opensource design data can do, is publishing STEP and native formats and what is available from the aforementioned (https://github.com/prusa3d/Original-Prusa-MINI/issues/34#issuecomment-680780459) documentation.

There is clearly a gap in tools for online open collaboration in mechanical design as compared to software development, and Prusa obviously does not take advantage of merge requests for mechanical design in this and the other github parts repositories; though increasing the amount of data in this MINI repo has been a step in the right direction.

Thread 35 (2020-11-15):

Extruder rear piece.

SgtKiLLx, 2020-11-15:
So, I need to do a new extruder rear piece for my Mini.. and.. the bigger hole that the brass fitting piece twists into, with larger spaced threads , I attempted to get it screwed in, and the whole thing split.

JohnnyDeer, 2020-11-18:
Hi @SgtKiLLx please contact our Support with this case. Chat in right down corner https://shop.prusa3d.com/en/ thank you.

SgtKiLLx, 2020-11-18:
> Hi @SgtKiLLx please contact our Support with this case. Chat in right down corner https://shop.prusa3d.com/en/ thank you.

Prusa chat support doesn't know shit. I don't see how they can help with this. There is no way that this piece was heated up and threaded in.

Closed 2020-11-18.

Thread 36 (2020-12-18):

Automatic skew correction.

riodoro1, 2020-12-18:
Are there any plans to bring skew correction to the MINI?
Ive noticed my printer is quite out of square (XY and YZ) and it’s not an uncommon problem on the internet.
Are the circles on the heat bed PCB actually there for this purpose and this would just need to be implemented in the code?

JohnnyDeer, 2021-01-19:
Hi @riodoro1, this issue should be in Prusa-Firmware-Buddy repository and is related to https://github.com/prusa3d/Prusa-Firmware-Buddy/issues/385. I´m closing this one.

Closed 2021-01-19.

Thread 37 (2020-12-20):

Bed heating up when unloading filament

hemdrup, 2020-12-20:
Why does the bed heat up when unloading filament? (This is not when printing, but directly from the home menu)

Prusa Mini+ , version 4.2.1

 https://youtu.be/dRz50qD_JEE

JohnnyDeer, 2021-01-13:
Hi @hemdrup, this issue should be in Prusa-Firmware-Buddy repository and its duplicate of https://github.com/prusa3d/Prusa-Firmware-Buddy/issues/706
I´m closing this issue.

Closed 2021-01-13.

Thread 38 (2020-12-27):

Request pre heating 5-10sec to prevent failsafe in cold climates

boobslappy, 2020-12-27:
I am requesting adding a 5-10 preheat to raise thermistors above threshold for those of us with our printing in cold areas. I’m having to use a blow dryer and don’t see why it couldn’t heat for a bit before checking thermistors. Could this feature be added? I’m on a prusa mini+. Thanks.

TickTock-, 2020-12-31:
Yes.  Please!  (or lower the threshold)

JohnnyDeer, 2021-01-13:
Hi @boobslappy this requirement should be in Prusa-Firmware-Buddy repository, please open it there according to the templates.  I´m closing this one here.

Closed 2021-01-13.

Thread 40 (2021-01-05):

Filament run out sensor failing to pause print

M8Harry, 2021-01-05:
Had a print run out of filament but the mini kept printing.

The sensor has done this once in the past (older firmware version) but it has saved a print as well on the previous version.

Sucks seeing 4hrs of a 9hr print wasted because the printer didn't stop. When loading new flament I tested the sensor when it detected filament the filament the menu on screen updated and i pulled it out it changed back. So the sensor is working when not printing but it's hit and miss during prints.
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

JohnnyDeer, 2021-01-18:
Hi @M8Harry, with this issue please contact our Tech Support (chat is on right side down ... https://shop.prusa3d.com/en/ ).

Closed 2021-01-18.

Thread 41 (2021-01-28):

Extruder Idler Arm Broke

Rockohaulic, 2021-01-28:
My Recommendation:
Update part per my design.  Extend length of arm slightly and have a thru-hole for the nut.  Place the nut all the way on the back side of the arm.
Then the plastic part would be under compression instead of tension!   No more failed parts!   :-)

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

JohnnyDeer, 2021-02-23:
Hi @Rockohaulic, thanks for your suggestion, we showed it to our developers.

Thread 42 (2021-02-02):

why can not connect mini to pronterface

Surealjedeye, 2021-02-02:
I have been trying to figure this out. I have easily connected 4 other branded printers to pronterface via usb. I connect the mini to my computer through usb. The computer recognizes it on Com 7. No matter the baudrate selected pronterface can not connect. I have tried everything me and my son can figure out. I just ended a chat with Prusa customer support and I was referred to this forum. Please help. I am so frustrated at the moment.

BogdanH59, 2021-05-25:
On Windows 10 I can connect Pronterface to MINI (I use baudrate 250000). Did you use mini USB port on MINI?

DRracer, 2021-07-30:
@Surealjedeye is your issue still relevant? Have you tried the latest FW 4.3.2-RC2?

zoltanbaranyai, 2022-12-15:
I have the same issue, any solution? Latest FW on printer and installed the latest driver from the prusa site.

Prusa-Support, 2023-01-03:
Hello. As mentioned in the Handbook, the micro USB port allows further third-party applications and custom uses.

> The micro USB port can be used to run third-party solutions

https://cdn.prusa3d.com/downloads/manual/prusa3d_manual_mini_en.pdf

This means that as of now, the use of it is not directly supported by Prusa Research. In fact, I'm afraid our drivers pack doesn't include any specific drivers for the correct functionality of the Prusa MINI via computer.
A user suggested some specific drivers in the Forum. Feel free to test this suggestion or take part in the discussion.
https://forum.prusa3d.com/forum/general-software-discussion/mini-and-pronterface-not-connecting/#post-489157

Other than this, apparently, there are two types of micro-USB cables on the market: charge/power-only cables and data/sync cables. The difference is apparently the power transmission capacity and the number of threads inside. You may want to make sure to use a cable suitable for data transfer.

Michele Moramarco
Prusa Research

DRracer, 2023-01-04:
Standard serial line is available on the MINI without limitations, but:
- baudrate needs to be set to 115200 bd
- you really need to use a data/sync micro-USB cable
- I'd recommend using firmware 4.4.0 and/or 4.4.1-RC1. There have been some issues with the serial line in the beta releases before 4.4.0

FYI: opening the serial line at 57600 bd shall be used for debugging - it makes the MINI send Marlin logs. This way you cannot issue G-codes into the printer.

The best way of checking whether the MINI connects to a computer is to look into the operating system logs and search for something like:
```
kernel: usb 1-1.2: New USB device found, idVendor=2c99, idProduct=000c, bcdDevice= 2.00
kernel: usb 1-1.2: New USB device strings: Mfr=1, Product=2, SerialNumber=3
kernel: usb 1-1.2: Product: Original Prusa MINI
kernel: usb 1-1.2: Manufacturer: Prusa Research (prusa3d.com)
kernel: usb 1-1.2: SerialNumber: CZPX.............
kernel: cdc_acm 1-1.2:1.0: ttyACM5: USB ACM device
```
This confirms, that Linux "sees" the new serial device - the MINI. From now on the serial port `/dev/ttyACM5` can be used to talk to the printer.

SimonTratter123, 2023-01-07:
I am able to use Octoprint with an Raspberry Pi with the micro USB port on the Mini. However I can't connect the mini to my computer to use Pronterface. Devicemanager does not find any device refering to the mini.

Prusa-Support, 2023-01-19:
Unfortunately the drivers are not included.
Please try the drivers suggested by the community on the forum.
Also make sure the micro USB port is not damaged in any way (wobbly, enlarged, detached or dry soldering...).

Michele Moramarco
Prusa Research

hkienle, 2025-02-12:
> micro USB port

Just to emphasize, because this may be easily missed: The USB-A port will not work, you have to connect to the USB Micro port that sits to the left of the USB-A port.

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
Source: https://help.prusa3d.com/article/octoprint-configuration-and-install_2182

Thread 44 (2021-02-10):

STOP button during Purge/Load/Unload

re490, 2021-02-10:
On my MINI+ (firmware 4.3.0 and prior) there is a STOP button displayed at the bottom of the screen during Purge/Load/Unload operations but it can't be selected.  It would be convenient to be able to stop these operations.

JohnnyDeer, 2021-02-11:
Hi @re490, this issue should be in Buddy FW repository and is duplicate of https://github.com/prusa3d/Prusa-Firmware-Buddy/issues/370 . I´m closing this one, thank you for understanding.

Closed 2021-02-11.

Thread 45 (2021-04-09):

USB stick occasionally becomes unreadable.

damiandixon, 2021-04-09:
Firmware: 4.3.1+2759

USB stick (one supplied with printer) is ejected correctly from Windows but occasionally becomes unreadable on insertion into printer and subsequently still unreadable on re-insertion into windows laptop.

Happened twice now. Both times reformatted.

raymate, 2021-04-09:
Try another stick, may not be the firmware. A few users have reported the supplied stick becomes bad or not work well. I didn't even bother using it. I got myself a Kingston branded one. DTSE9, I have two versions one 32GB and an older 4GB. The 4GB work without any issues. The 32GB sometimes does not show up in the printer. This is what he latest firmware might fix as its USB driver related. Most say use a stick no bigger than 8GB. I tend to agree with current stable firmware. But getting hold of small USB sticks is becoming hard, I looked and I would need to resort to eBay to get a 4GB stick now days. So I hope once this latest firmware becomes live it will let me use my 32GB stick with no issue.

damiandixon, 2021-04-21:
A new 4GB USB integral drive seems to be working fine.

Closed 2021-04-21.

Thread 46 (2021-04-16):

Change Filament confirmation

Freland, 2021-04-16:
When changing speed it it quite easy to press "Change Filament" in the menu. Which is quite annoying. An easy confirmation "Yes/No" would solve this "issue" easily.

JohnnyDeer, 2021-05-18:
Hi @Freland, you are in wrong repository this is FW related and it´s duplicate of https://github.com/prusa3d/Prusa-Firmware-Buddy/issues/1387. I´m closing this issue.

Closed 2021-05-18.

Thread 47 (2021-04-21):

Problems with Hostnames in firmware 4.3.1 (Using more than one Prusa mini)

waltercwitt, 2021-04-21:
Repost from prusa printers forum
"
Hello,

I've been chasing this issue around for quite some time now, but it appears that no-one else is having a similar issue. At work, I've setup 2 Prusa MINIs with both of them connected to our network via the same ethernet switch. I set them up with the hostnames, http://prusamini1 and http://prusamini2 to make it easier for people to remember where to check the status of there prints.

The problem I'm having is, sometimes after restarting the printer, the hostname gets wiped, and the printers can only be accessed by there IP address, and in rare cases, one of the printers will take the hostname of the other. This was actually happening a bit before firmware 4.3.0, but it seems to have gotten far worse after updating them.

During my troubleshooting of the issue, I discovered some very odd things that the printers where doing:

- If, during power on, there was a flash drive that had a lansettings.ini file on it plugged into the machine, It would overwrite it's current settings with the ones in the file. (I'm pretty sure this is what was causing one printer to take the others hostname)
- When I save the LAN settings to a flash drive, the hostname it saves is always blank, even when the hostname is set and working. (I am not allowed to set as static IP for the printers at work, so I can't verify if any of the other settings are returning default values as well.)
- When I load the LAN settings from a flash drive using the menu, it very rarely actually works, meaning I have to use the bootup method in my first point to fix it. (Again I have only ever tried changing the hostname, all the other settings I have to leave as default as per my works IT network policy.)

Aside from that, I'm finding it quite annoying that the printer will display every other network setting in the LAN settings menu, EXCEPT the hostname, so in order to check if I've successfully fixed it, I have to walk all the way back to my computer on the other side of the building to test it.

I've made sure that I don't have a lansettings.ini file on any of the flash drives I use, but they will still sometimes just forget the hostnames anyway. and then I have to save a new file to a flash drive, modify it on my computer, turn off the printer, and boot it up with the flash drive inserted to fix it, and sometimes, it doesn't work the first time.

Has anyone else had similar issues with there printer forgetting LAN settings since the 4.3.0 update?
"

okaerin, 2021-04-25:
@waltercwitt This sounds rather unpleasent. Unfortunately this is the wrong repository. It only contains the hardware/design parts. The firmware of the prusa mini is maintained at [https://github.com/prusa3d/Prusa-Firmware-Buddy](https://github.com/prusa3d/Prusa-Firmware-Buddy). I would suggest that you close the issue here and post it over there [https://github.com/prusa3d/Prusa-Firmware-Buddy/issues](https://github.com/prusa3d/Prusa-Firmware-Buddy/issues) . I hope that the prusa people maintaining that can figure that one out.

waltercwitt, 2021-04-27:
Oh, sorry, I was sent here by a Prusa support person. I'll do that now

Closed 2021-04-27.

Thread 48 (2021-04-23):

USB Hub not working

passteinforth, 2021-04-23:
Hi,
I want to use a USB Hub to connect more USB devices to the Mini. I use this Hub https://www.alternate.de/i-tec/USB-3-0-Metal-HUB-4-Port-USB-Hub/html/product/1524373 and connect it to the USB-A Port of the Mini. The little LED of the Hub turns on, but when connecting the original USB stick to load print files, nothing shows up and in the main menu it still says 'no USB'. The USB stick is the only device plugged into the hub at this moment.
When connecting an Arduino Nano to the USB hub, it gets powered as intended (the Nano controls a humidity sensor for a drybox and a 7-digit displays and only draws some power, no data connection).
The second USB port of my Mini is blocked by Octoprint/Raspberry Pi 4, so I cant use this to power my humidity sensor/Arduino.

JohnnyDeer, 2021-05-17:
Hi @passteinforth, USB hub is not supported by MINI, this won't work even if you plug in just one USB stick. I´m closing this issue as invalid.

aargonz23, 2022-03-24:
@JohnnyDeer @josefprusa why wont the mini+ support a hub? I tried a switcher and that wouldnt work either. why not have it wirelessly connect? arent there more options for the other printers? im not sure I understand the issue with setting up the mini to be more convenient than just swapping the USB drive out constantly. I know there are options to connect a raspberry Pi to a mini but they're not exactly easy to come by this year. I've tried and they sell out before you even think to check. I know its not a massive issue but better options would be massively appreciated by the mini+ community as a whole.

JakoobCZ, 2022-04-06:
Hi guys, the MINI+ USB port was designed to support a USB flash drive. Powering any other external device (like USB hub) was not planned nor tested. Getting the USB hub to work including full power would require HW adjustments to the board and changes to the firmware.

Closed 2021-05-17.

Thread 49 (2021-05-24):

Feature request: show number of hours spent printing

DanidCH, 2021-05-24:
As to help keep the printer well maintained I would appreciate having a menu entry allowing to have some statistics on how much time the Prusa Mini printer has spent printing. It would allow to check how fast you got to 100 hours tick.

JohnnyDeer, 2021-06-22:
Hi @DanidCH, this request should be in firmware repository and there already exist https://github.com/prusa3d/Prusa-Firmware-Buddy/issues/366. I´m closing this one as duplicate.

Closed 2021-06-22.

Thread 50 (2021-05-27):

Lead Screw not called out on Z-Axis BOM

pltaylor, 2021-05-27:
The specs for the lead screw are missing from the Z-Axis BOM on https://github.com/prusa3d/Original-Prusa-MINI/blob/master/BOM/Z-AXIS.md

JohnnyDeer, 2021-06-22:
Hi @pltaylor, thank you for your comment. We will add specs of lead screw to X-Axis BOM where is secured trapeze screw.

Prusa-Support, 2022-05-10:
Hello! Sorry for replying so late to this thread. The Z-axis motor leadscrew specs are currently within the "MINI Z-axis motor" link, which points to the documentation of all the MINI motors: https://github.com/prusa3d/Original-Prusa-MINI/blob/master/DOCUMENTATION/ELECTRONICS/mini-motor-kit.pdf. Within that page, there is the Z-axis motor documentation, which includes the leadscrew and trapezoid nut specs.

Alessandro Pantaleo
Prusa Research

Closed 2022-05-10.

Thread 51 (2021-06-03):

Filament sensor susceptible to jamming open

murk-sy, 2021-06-03:
I've encountered this issue on one of my printers, even though it worked perfectly fine out of the box. Issue #40 may be related.

Either due to deformation or conflicting clearances between the pcb and the arm, the following pieces jammed and were stuck open (as "filament present"). This caused the filament sensor to not detect filament run out.

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

This was relatively easily rectified by just sanding the outer surface of the arm. However, why the issue appeared in the first place is a mystery. The printers are kept in a semi-enclosure, though I doubt ambient temperatures of ~30°C would cause some deformation due to stress being relieved. Maybe? I have tried a test piece printed in PLA and although I couldn't really see a dimensional difference, that one worked fine.

Making it slightly more pointy on the outside and straight on the inside (it interfaces with a flat surface anyway) may avoid this issue. Depending on the position of the sensor beam itself, top/bottom points of the wedge could also be chamfered slightly to avoid elephant foot related interference.

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

JohnnyDeer, 2021-06-22:
Hi @murk-sy, thank you for a well maked suggestion. We will investigate it and improve in next version of filament sensor.

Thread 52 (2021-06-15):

Design improvement - power cable guide

Fliens, 2021-06-15:
A small guide on the back of the printer electronics base for both cables so LAN and power.
This would help a lot when plugging the cables into their sockets while not being able to see the back.

My printer is on top of a shelf and I can't see the back, so it's very difficult to align the cables when plugging them in.
These guides could be a small beveled circle and square, so that the back of the box is no longer flush with the sockets.

This would protect the cables and the box and would also help impaired people to set up the printer

JohnnyDeer, 2021-06-22:
Hi @Fliens, thank you for suggestion. We will keep it on mind for next possible iterations.

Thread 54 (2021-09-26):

After upgrade: PINDA gathered data not being used unless sheet is selected

unxs0, 2021-09-26:
Bed leveling data is not used, even if doing first layer calibration if you have not selected a sheet profile previously.

I guess this happens only after upgrade from pre 4.3.0, where sheet profiles did not exist and the hapless user did not RTFM (does the upgrade doc explain this?)

Of course this is very problematic since it leads users to check PINDA and bed hardware.

Cheers for a great product that will only get better!

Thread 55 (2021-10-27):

Early Tuning Displayed but Not taken for control

funtomaas, 2021-10-27:
I used actual FW 4.3.3 , when I started the plot I tuned the heat of the heatplate very soon to 90 (turning and pressing Button to accept). The demanded heat changed in the tuning Part of the screen, but when the plotting process startet: the temperature stayed standard 85 AND the demanded Temperature (right below) did the same 85. I had to activate the tuning again as of I Never did before- but the Parameter in the tuning list still showed my wanted Temperature. ( no big issue, but good to know). Regards ( great project, thx!!) Funtomaas. :)

funtomaas, 2021-11-14:
shifted to Prusa firmware buddy  by myself

Closed 2021-11-14.

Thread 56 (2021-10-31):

putting heatbed to heat with unplugged heatbed heater won't reboot the printer

kevinpita, 2021-10-31:
I have seen [thomas video ](https://www.youtube.com/watch?v=eGUPBoDxmKk) and I have done the 3 tests, thermistor tests work ok, but doing the heater one won't work, it should stop heating or reboot the printer, but nothing happens, it just stay 30/80 for example

Prusa-Support, 2022-05-05:
Hello! I am sorry for the late response to this issue.

Which submenu selection was selected more precisely?
Settings>Temperature>Heatbed
Start>Print
Preheat>Filament Type

How much time was it staying in the 30/80 screen without preheat error or thermal runaway error? I have to confirm it, but from a check I have done, it would take 4 minutes for thermal runaway on the heatbed to activate. Was it run that way for so long? Would it trigger the error after that time?

Let me know, in case of need we can review this in more detail.

Alessandro Pantaleo
Prusa Research

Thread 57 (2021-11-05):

[ENHANCEMENT] better heatbreak

SnickCH, 2021-11-05:
Printer: Mini /Mini+

**Problem**
There is a reason why bondtech and others sell heatbreak upgrades for the Mini and Mini+. The actual heatbreak has a borehole that goes way to near to the nozzle. Another problem is the design, that is streight and has no cutout to minimize the heat travel. Therefore a lot of user experience a problem with the heat break.

- printing on high temperatures may defor the PTFE tube
- if the PTFE tube is replaces and not cut "perfectly" it has a gap that will easily filled with melted filament
- Other printing quality issues that are related to the heatbreak

A good overview and explanation is in this video:  https://youtu.be/5CLnF0a9vwY

Solution
There would the following things to improve it
1. The borehole shouldn't be so deep. Like other allmetal hotends (like the micro swiss for Creality printers).
2. A cut out just after the heatblock leaves the heatblock
3. Use titanium alloy that has better termic blocker

Points 1-2 is used by the bondtech upgrade that is sold for about 20 USD. This upgrade should nod cost much for if you produce it in your sclae. Points 1-3 is used by the brozzle upgrade that is sold for about 25 USD.

In the picture: Bondtech design (left), original (right). The credit for the picture (I took a printscreen at 6:55): https://www.youtube.com/watch?v=5CLnF0a9vwY

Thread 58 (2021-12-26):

[ENHANCEMENT] Dual Gear extruder

SnickCH, 2021-12-26:
It would be great, if the Prusa mini/mini+ would receive an extruder upgrade with dual gear. There is a reason that Bondtech can sell many upgrades for the Prusa mini and even the community on Thingiverse is providing new extruders for the mini. With an official extruder it would make our life much easier.

The main problem with the actual extruder are the following in my opinion

- soft filament can't be printed, because the gears will rasp the filament and cause that it will be stock in the extruder
- the gear teeth are to fine /small
- Not all kind of flex Filament can be printed
- precision could be improved
- Hard to clean. It must be disassembled to be cleaned. Filament that was rasped gets stuck inside

With eSun and Prusament I didn't have any problems. As soon as I used a softer filament, I had to clean the whole extruder (and also the hotend, because of the clog that was produced). If you compare the price for a dual gear extruder it would not cost much more if it comes on the stock printer. If you have to upgrade it later, it is an expensive task.

Example: https://www.thingiverse.com/thing:4179460

Prusa-Support, 2023-08-25:
Thanks for your suggestion.

The printer is Open Sorce, hence easily modifiable.
Officially we can't offer direct support for mods but we love to see the active members of the community sharing projects and ideas and surely we won't ignore them.
As far as I know, there aren't new model iterations in the current plans but we are listening.

Michele Moramarco
Prusa Research

KlausKraemer, 2023-08-27:
Hi Michele,
it's not about easy modifying - it's about quality!
Best regards
Klaus

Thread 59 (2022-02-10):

[ENHANCEMENT] Live Z option while printing at print screen

OopAck, 2022-02-10:
Requesting a Live Z option while printing and at print screen to the firmware.

Martenz, 2022-05-17:
Do you mean to have also the Z level number together with the Z level in mm on the lcd screen? If so I totally agree, I found I use the printer with usb most of the time and I'd like to know which level is printing.
Something like percentage of the print and level printing:

83% - 272/326

Prusa-Support, 2022-05-17:
Hello! Thank you for the request. @OopAck can you please expand on the request? Did you mean the Live-Z adjust in the format -0.123 or more the percentage as @Martenz mentioned?

If it was the first case, was there an issue with inconsistent Live-Z adjust values throughout the same print or across prints? Let me know in that case, we can expand on it.

Alessandro Pantaleo
Prusa Research

OopAck, 2022-05-17:
Figured out.

Closed 2022-05-17.

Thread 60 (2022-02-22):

Please provide us a way to manually adjust the nozzle height

bhs67, 2022-02-22:
For the Original Prusa Mini+ => As a customer request, please provide us a way to manually adjust the nozzle height (not part of a calibration).

Prusa-Support, 2022-05-02:
Hi. You can do this using the First Layer Calibration (Calibrations menu) feature to adjust the Live Adjust Z value.

Closed 2022-05-02.

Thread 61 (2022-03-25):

Rear Fan Noise

Punksterz, 2022-03-25:
Irregular, loud rear fan noise not caused by debris continues to be a mystery.

Prusa-Support, 2022-05-05:
Hello! Thank you for the report and sorry for the late response. Was this resolved in the meantime?

The noise on print fan is almost certainly caused by mechanical aspects, can you please send me a video to better assess it?

Let us check if there might be room to further tighten this bolt: https://cdn.help.prusa3d.com/wp-content/uploads/2021/01/42a84b3ad1a2a586_painted.jpeg, or if the fan might be physically not fixed in place. Also, with the printer still off and cold, let us attempt very gently pushing the fan rotor back in place, would it "click back in place" and would that improve the noise level?

If not, it might be related with premature wear of the fan itself. In that specific case, please contact me via email info@prusa3d.com, mentioning "attn: Alessandro" in the subject, I'll help you with the resolution.

Alessandro Pantaleo
Prusa Research

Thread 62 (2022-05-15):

Documentation for LCD board missing rotary encoder.

eivory, 2022-05-15:
Original-Prusa-MINI/tree/master/DOCUMENTATION/ELECTRONICS missing specification for rotary encoder.

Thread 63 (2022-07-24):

Prusa Mini+ Z-top R1.1 - Extra Height

seifer69er, 2022-07-24:
Based on 3d file uploaded to PRUSA Printers,
https://www.printables.com/model/202467-prusa-mini-z-top-r11-extra-height
and
https://www.printables.com/model/179537-prusa-mini-z-axis-extra-height-adaptor

There is an issue that the extruder assembly owls on the Z axis top.
This in turn is not the true end stop of the PRUSA MINI+.
By removing material of the z top to allow the extruder to pass through, this in turn allows the prusa mini to gain an additional ~4-5mm in z height.
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

Prusa-Support, 2022-07-25:
Hello! Thank you for your feedback. If I understood correctly, the issue was only with the parts in the link, but these are not our original parts - our original MINI/+ printable parts are in this folder: https://www.printables.com/model/57214-mini-printable-parts, would the issue be there also with our original parts?

Let me know, in case of anything to further review, do not hesitate to ask.

Alessandro Pantaleo
Prusa Research

seifer69er, 2022-08-01:
Hi there, yes, the issue is with the original parts, the Z top will need to be trimmed as per the link attached R1.1.
I can provide the step file or any additional clarity as required,

seifer69er, 2022-08-02:
Hi there,

That is correct, a minimum of 5mm additional z axis height is achieved

Prusa-Support, 2022-08-02:
Thank you for the confirmation! OK, tagged it as enhancement, no guarantees it would be implemented, and likely it won't, but will be there for devs to further review in case. Thank you once again for the suggestion.

Alessandro Pantaleo
Prusa Research

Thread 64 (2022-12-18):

Force reset required if USB removed on print preview

hamdeli, 2022-12-18:
If USB is removed whilst the printer is displaying print preview, navigation is blocked. You cannot navigate to "Back" and you are forced to reset to resume any printer function.

I have not tested on any other firmware/bootloader than below:
- Firmware: 4.4.0
- Bootloader: 2.0.2

hamdeli, 2022-12-18:
closing issue as this is not the correct repository to report this. It has been moved to the firmware repo.

Closed 2022-12-18.

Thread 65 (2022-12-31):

Random Print Positioning

KlausKraemer, 2022-12-31:
Is it thinkable that prints could be printed at random positions?

Most prints are printed in the middle of the print bed. So naturally the wear on PEI coating is concentrated at the middle of the print bed. And it's not even restricted to the print bed. It's the same with guide rails and tooth belts.

So randomly placing a print could take some wear of multiple printer parts.

Prusa-Support, 2023-01-31:
Thanks for the suggestion but please mind the print positioning solely depends on Prusa Slicer.
This issue shouldn't be posted here but in [prusa3d/PrusaSlicer](https://github.com/prusa3d/PrusaSlicer) repository.
Also please notice, it is a duplicate of issue https://github.com/prusa3d/PrusaSlicer/issues/320.

Other than this, I would recommend printing in the middle of the bed, and rather avoid printing close to the edges if you can.
Heat dissipation is stronger near the edge, so the adhesion of the object could be weaker, and the object cooling could be a bit too fast too. In fact, often it helps if you print large objects (reaching the edge) with a slightly higher bed temperature.

I hope you will find my advice useful.
Now please allow me to close this issue as unrelated to this repository and as a duplicate.

Michele Moramarco
Prusa Research

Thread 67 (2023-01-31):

MINI+ Suggestions/Enhancements: time remaining option, menus, bed heating, purge, PrusaLink

re490, 2023-01-31:
MINI+ Wish List / Suggestions:

1) 4.4.1 Firmware changed to showing Clock time for print finishing;   Consider option to toggle print time between clock time or hr/min remaining   (I prefer knowing hrs/min remaining, not clock time)

2) Make Front knob rotation consistent in Menus:  in Menus, clockwise moves selection down, but in adjusting Z-height, clockwise moves the nozzle up.

3) Why does Heated Bed need to heat up when loading/unloading filament?    (doesn't save print time)

4) during filament loading, the purge menu has a STOP button that doesn't work and no way to change the duration of purge.  Consider a menu item for nozzle purge that allows user to manually start/stop a purge for any amount of time between prints or during filament loading instead of a fixed duration of filament purge.

5) If you send a file to the printer using Wifi/PrusaLink while another file is printing, the currently printing file name in PrusaLink changes to the name of the sent file

thanks!  Just some ideas for consideration.

sander1095, 2023-02-05:
Hi! I am in no way affiliated with this project, but I would recommend creating seperate tickets for each of your bullet points.

This way they may be discussed individually, or closed if it is a duplicate of an existing item!

Some of these are clearly bugs and seperating them makes it easier for the devs to find and prioritize them.

I definitely agree with point 1 and 3 though! I hope that can be implemented!

Prusa-Support, 2023-03-08:
Please post every bug report or feature request as a separate issue, but first please check among the already existing issues.
If an issue already exists, please don't create a new similar one but comment in the existing thread.

Allow me to briefly comment on your points and close this issue as invalid.

1. Already existing issue.
2. I personally find it intuitive as it is now, this is a matter of personal preference though. Feel free to open an issue, but also mind this is simply a conventional choice and many customers may not appreciate a sudden change of trend
3. Already existing issue.
4. Already existing issue.
5. Already existing issue.

Michele Moramarco
Prusa Research

Closed 2023-03-08.

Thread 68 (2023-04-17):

Out of memory issue while idle (malloc: out of memory)

MrTrick, 2023-04-17:
I don't have the exact "steps to reproduce" here, but as best as I remember:

1. The printer was left on for about 1 week. (Prusa Mini+ with the wifi add-on board)
2. Maybe 3-4 prints had been sent to it via wifi during that time, printing for a small percentage of the total uptime.
3. When finished printing, I run the "unload filament" sequence.
4. The printer had been left alone for at least 24 hours prior to the crash.

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

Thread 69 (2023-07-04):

Ideas for Improvements

inieto, 2023-07-04:
- "Probing point 1...16/16" could be done while heating the nozzle and bed in parallel. It's sequential actually and it take so many time
- "Probing point 1...16/16" waits the nozzle to cool down to 170ºC. It could actually be done without setting the temperature to 170ºC. Let's imagine the following example:
· First we wait from ambient temperature to 260ºC to load some filament.
· Then we have to wait for cooling down to 170ºC to make the probing point procedure
· After that, we have to wait again to heat up to 260ºC to start printing
We end up waiting 3 heat-cool-heat cycles!

- Loading filament should not wait for bed heating: we only need to wait for the nozzle to heat, not the bed.. This could save us some minutes.

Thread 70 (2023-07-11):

Press Knob before changing filament

dimensionarg, 2023-07-11:
Hi!

I have a small MK3 and MINI Farm, and i saw a diference when changing filaments: MK3 ask you to press knob before taking the filament out, but the MINI doesn't. This is a problem because, if you are not near to the printer and you dont take the filament out,  the tip (that is still malleable because it cames from the hotend/nozzle) starts to cold down but the gravity make the tip to bend/fold down, so it forms like a "hook", and this makes the filament to get stuck. If you pull with some sthengh the filament gets out, but some part of the filament breaks and a small piece starts to accumulate in the extruder and this bring other problems.

Can i fix this from the gcode? or will need to wait from next firmware update (only if you think this is a problem)

Thanks!

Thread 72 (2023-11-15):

Mini regularly goes "Malloc - out of memory " when using remote upload/delete

Moyrn, 2023-11-15:
Mini regularly goes "Malloc - out of memory " when using remote upload
- i now manage my files on MINI USB key using "prusa link"
- i delete an upload files
- sometimes (twice today), the printer goes "red & buzzing" with message "Malloc - out of memory "
- last time happened when I launch a print on the printer, on a file i uploaded remotely

From my experience, this is more due to remote-deleting files than uploading but i may be wrong.
My USB is not full
reseting the printer, and launching the print is fine
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

See picture

Cheers,

Wilfried

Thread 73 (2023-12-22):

Disabled heating on Prusa Mini leads to nozzle blockages

SeppeDR, 2023-12-22:
Hi there,

I'm using the Prusa Mini for over 2 and a half years, but recently for mass production of parts, about 200 a day. This uses a lot of filament. As there is no automatic filament switching when the filament is finished, I often awake in the morning to the message that the heater has been disabled after 30 minutes of inactivity.

This is a great feature, however, in those 30 minutes, my pla filament gets cooked in the nozzle. I have 4 high flow nozzles that have become completely useless as they are extremely difficult to clean and cold/warm pulls do not work on them. Needling is the only solution, however, risks of ruining the internal structure of the nozzle. That's about a 100 euros in the trash by now.

I wonder whether the 30 minutes of time is not excessive? It does not take long for the heater to reheat the nozzle to the right temperature. And if it would be switched off after a few minutes, I'm sure the pla wouldn't be cooked.

Just letting it know, and hoping this could be perhaps changed if future firmware, or a setting for the user to choose.  Of course I know that there is some excellent solutions on my end as I could take more care to replenish the filament before it runs out, but that would mean a lot of spools with a little bit of filaments left or just a lot more work in general to make sure the nozzle is not getting blocked.

I had bad batches for over 2 weeks, with problems worsening. Took me a while to figure everything out. Could also help with less people having to contact Prusa support for clogged nozzles.

Anyways, thanks for reading. xx

3d-gussner, 2023-12-27:
@SeppeDR Please close this issue here and open it in https://github.com/prusa3d/Prusa-Firmware-Buddy firmware related github repository.

I am not sure if [`M86`](https://reprap.org/wiki/G-code#M86:_Set_Safety_Timeout)  is active on the Mini but you can try it to add this to your gcode files and PrusaSlicer profiles.
It has to be added to each gcode file as after reset or power on the default values are active again.

Closed 2023-12-27.

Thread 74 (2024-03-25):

Grafical Incorrect refreshing of the display during cool-down

Hubseba, 2024-03-25:
If you press the Cooling option under Control; Temperature, the temperatures are not wiped out correctly.
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

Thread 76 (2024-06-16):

missing filament sensor ipt files

sl1pkn07, 2024-06-16:
Hi

missing all parts of filament sensor ipt files in printed parts sources

greetings

sl1pkn07, 2025-02-26:
for the mini, they ship stp, stl and inventor(ipt) files, that files is missing

D2R-Gimli, 2025-02-26:
The ipt files are missing so native edits are not possible, yes.
You can still use the stp files as neutral cad files and edit or print them as replacement.
Years ago i've made also the full assembly based on the original parts.

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

sl1pkn07, 2025-02-26:
yea, but that is not the point. the point is that ipt files, like the all pieces in this project, are missing. no more, not less

the format you can use instead is irrelevant.

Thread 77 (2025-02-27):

Bed position during filament change leads to debris in printer

EmilBjorn, 2025-02-27:
The default bed position during filament change and purging causes ooze out and purge to risk falling beneath bed. Adding one Y move to the procedure would mitigiate this severely.

When changing filament, the X-axis homes itself and is positioned at a specific spot. However the Y-axis is not moved.

Filement is often changed after a print is finished and the bed is positioned all the way to the front.

This means the nozzle is positioned above the back edge of the bed. During the procedure, small bits of both new and old filament will exit the nozzle and can fall off on its own. Inevitably this can end up beneath the bed and inside the printer.

However by just moving the Y-axis to the middle position this is much less likely to happen. Any ooze out and purging will almost definitely be sitting on the bed, for you to pick up and throw out, without having to fish for it among the Y belts and pulleys.

Small problem - even smaller fix :)

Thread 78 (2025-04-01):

Top portions being treated as tree supports thin poor quality parts

FeralDG, 2025-04-01:
Been dealing with this one since the input shaper went live on the Mini and I've finally had enough of it. It seems as if the tops of certain small items are being treated as tree supports. This is a reproducible on any of the Prusa Minis in my fleet. Currently I run 6 of them and they all do it. I have gotten around the issue by moving problematic work to other machines but enough is enough. Input shaper is mature. Let's get this fixed.

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
Example of issue

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
Example of good part on same plate, different location. (There were 4 parts total, the part in the front right corner had the issue on multiple machines.)

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
Different machine, same issue.

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
Different angle

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
Good part, different angle

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
Wider image of full plate. Note bad part in front right.

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
This image is to satisfy the inevitable "it's the gcode" response. The item on the left was printed all by itself. I think 3 different minis, two different files. The middle item was again printed by itself. The item on the right came from a MK4 and turned out fine.

I was printing 28mm miniatures with these Prusa Minis & a .25 nozzle prior to the input shaper update. As soon as that update dropped printing acceptable miniatures was no longer possible. And it still isn't. I keep hoping the next firmware update will solve the issue. So far it hasn't. So here we are.

These machines range in age from newer to a older. Some with brand new hot ends, some with new extruder drive gears. All have had the PTFE tubes replaced numerous times over their life.

FeralDG, 2025-04-03:
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

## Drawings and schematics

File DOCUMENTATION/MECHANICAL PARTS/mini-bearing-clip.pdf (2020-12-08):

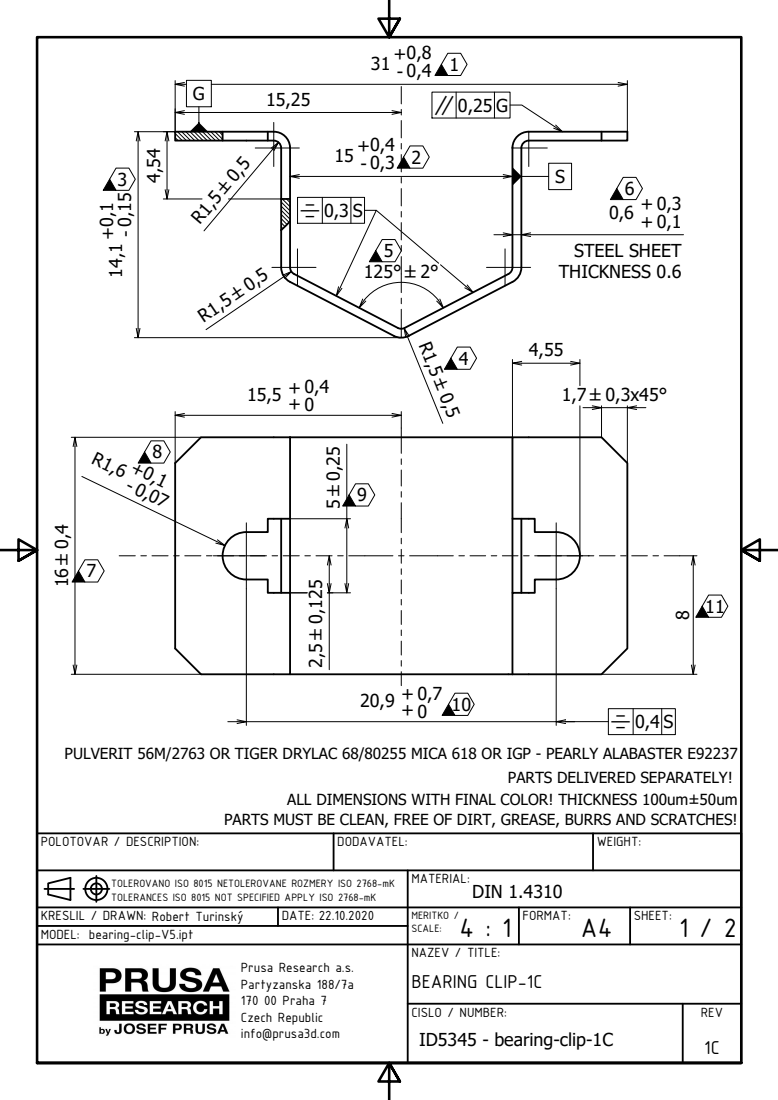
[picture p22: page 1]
STEEL SHEET THICKNESS 0.6

PULVERIT 56M/2763 OR TIGER DRYLAC 68/80255 MICA 618 OR IGP - PEARLY ALABASTER E92237

PARTS DELIVERED SEPARATELY!

ALL DIMENSIONS WITH FINAL COLOR! THICKNESS 100um±50um

PARTS MUST BE CLEAN, FREE OF DIRT, GREASE, BURRS AND SCRATCHES!

POLOTOVAR / DESCRIPTION: | DODAVATEL: | WEIGHT:

TOLEROVANO ISO 8015 NETOLEROVANE ROZMERY ISO 2768-mK
TOLERANCES ISO 8015 NOT SPECIFIED APPLY ISO 2768-mK

MATERIAL: DIN 1.4310

KRESLIL / DRAWN: Robert Turinskë | DATE: 22.10.2020 | MERITKO / 4 : 1 SCALE: | FORMAT: A4 | SHEET: 1 / 2

MODEL: bearing-clip-V5.ipt

Prusa Research a.s. Partyzanska 188/7a 170 00 Praha 7 Czech Republic info@prusa3d.com | NAZEV / TITLE: BEARING CLIP-1C

CISLO / NUMBER: ID5345 - bearing-clip-1C | REV 1C

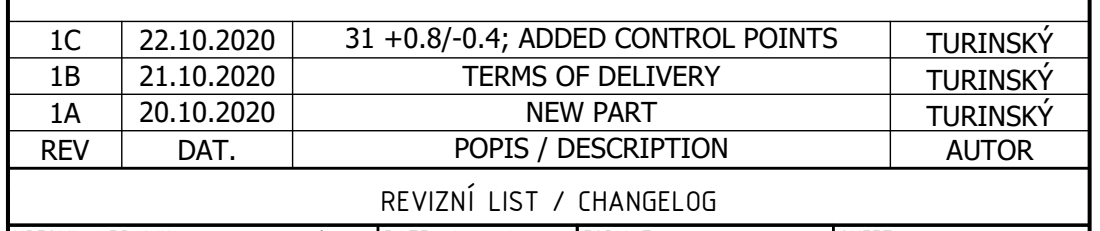
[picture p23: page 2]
KRESLIL / DRAWN: Robert Turinskë; DATE: 22.10.2020

1C | 22.10.2020 | 31 +0.8/-0.4; ADDED CONTROL POINTS | TURINSKé
1B | 21.10.2020 | TERMS OF DELIVERY | TURINSKé
1A | 20.10.2020 | NEW PART | TURINSKé
REV | DAT. | POPIS / DESCRIPTION | AUTOR

REVIZN LIST / CHANGELOG

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

CISLO / NUMBER: ID5345 - bearing-clip-1C | REV 1C

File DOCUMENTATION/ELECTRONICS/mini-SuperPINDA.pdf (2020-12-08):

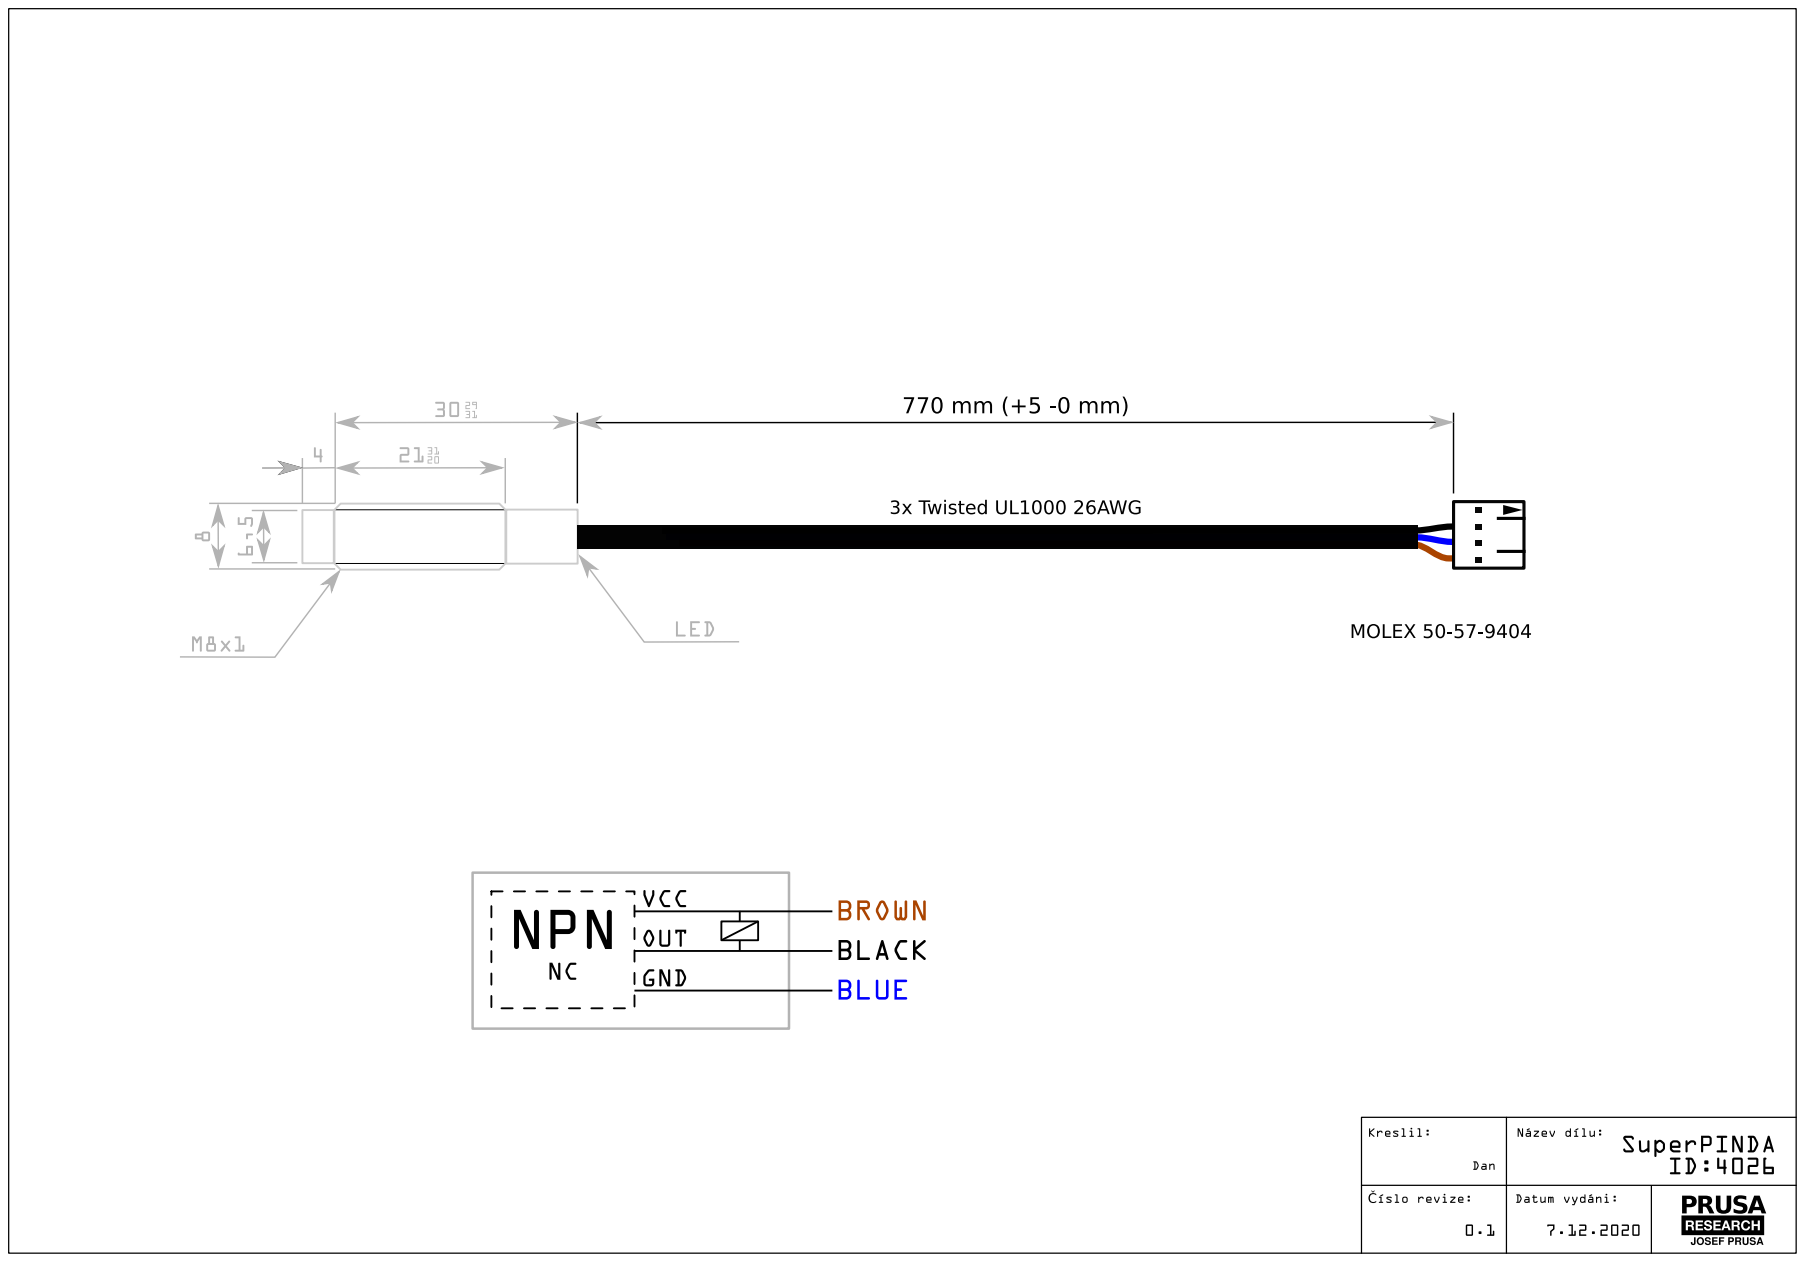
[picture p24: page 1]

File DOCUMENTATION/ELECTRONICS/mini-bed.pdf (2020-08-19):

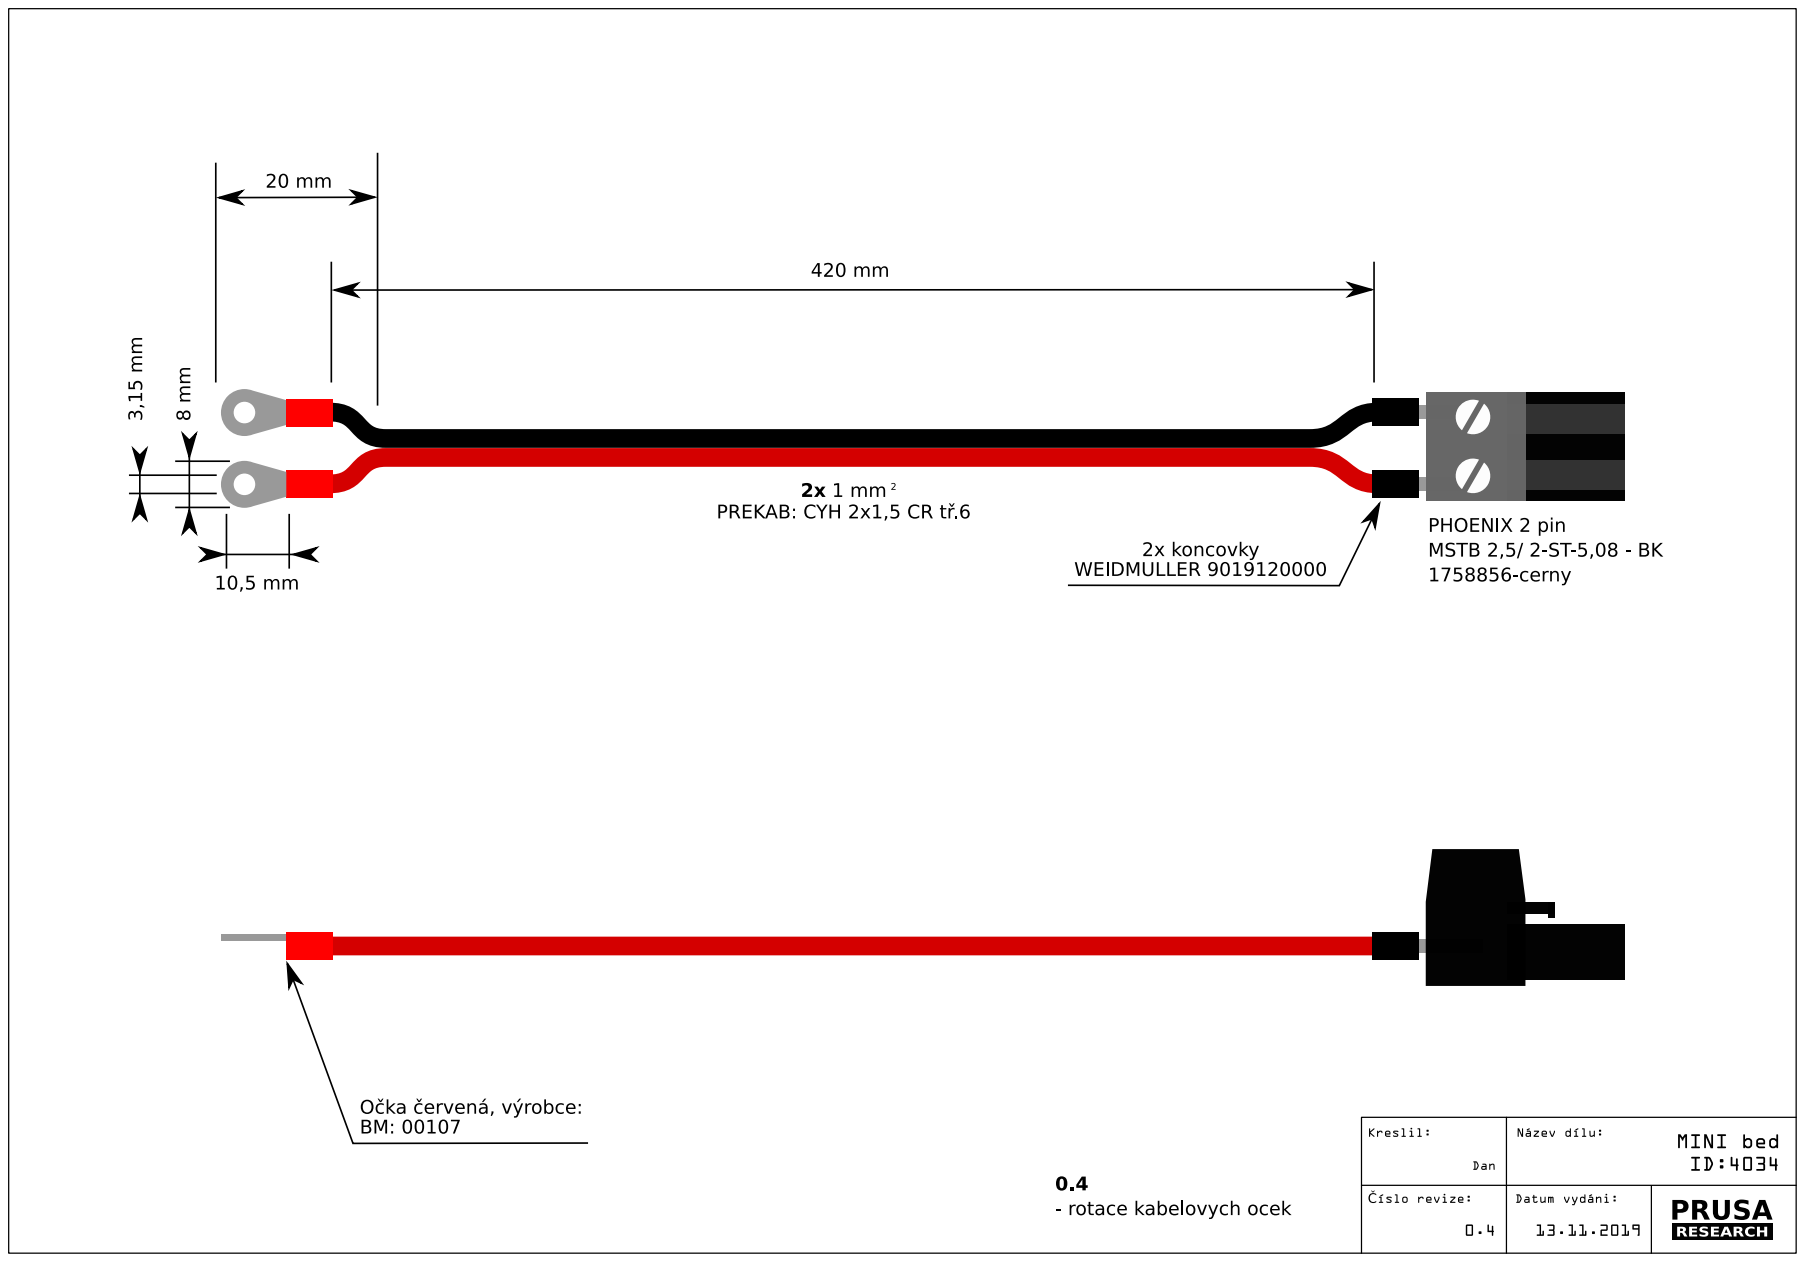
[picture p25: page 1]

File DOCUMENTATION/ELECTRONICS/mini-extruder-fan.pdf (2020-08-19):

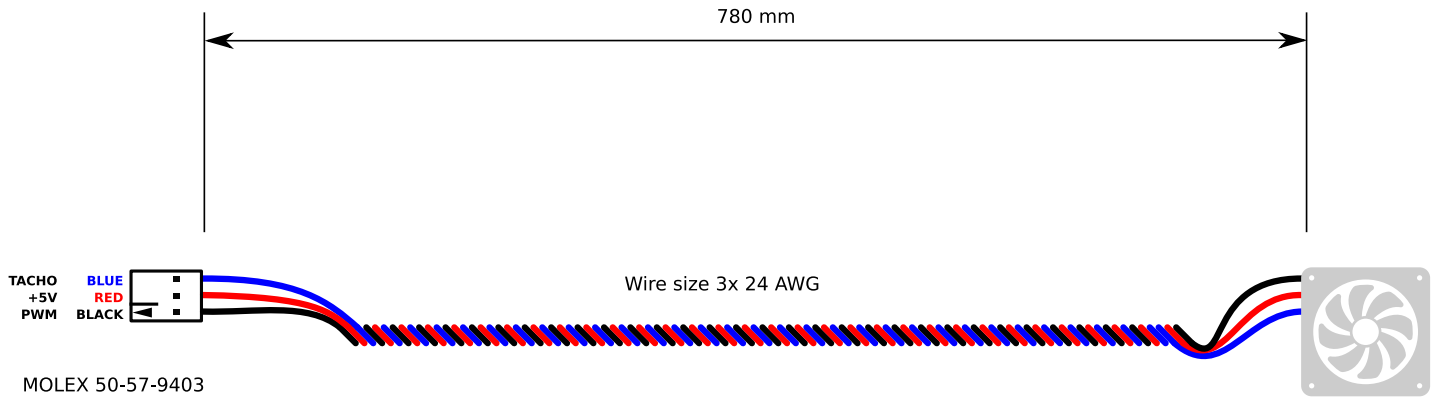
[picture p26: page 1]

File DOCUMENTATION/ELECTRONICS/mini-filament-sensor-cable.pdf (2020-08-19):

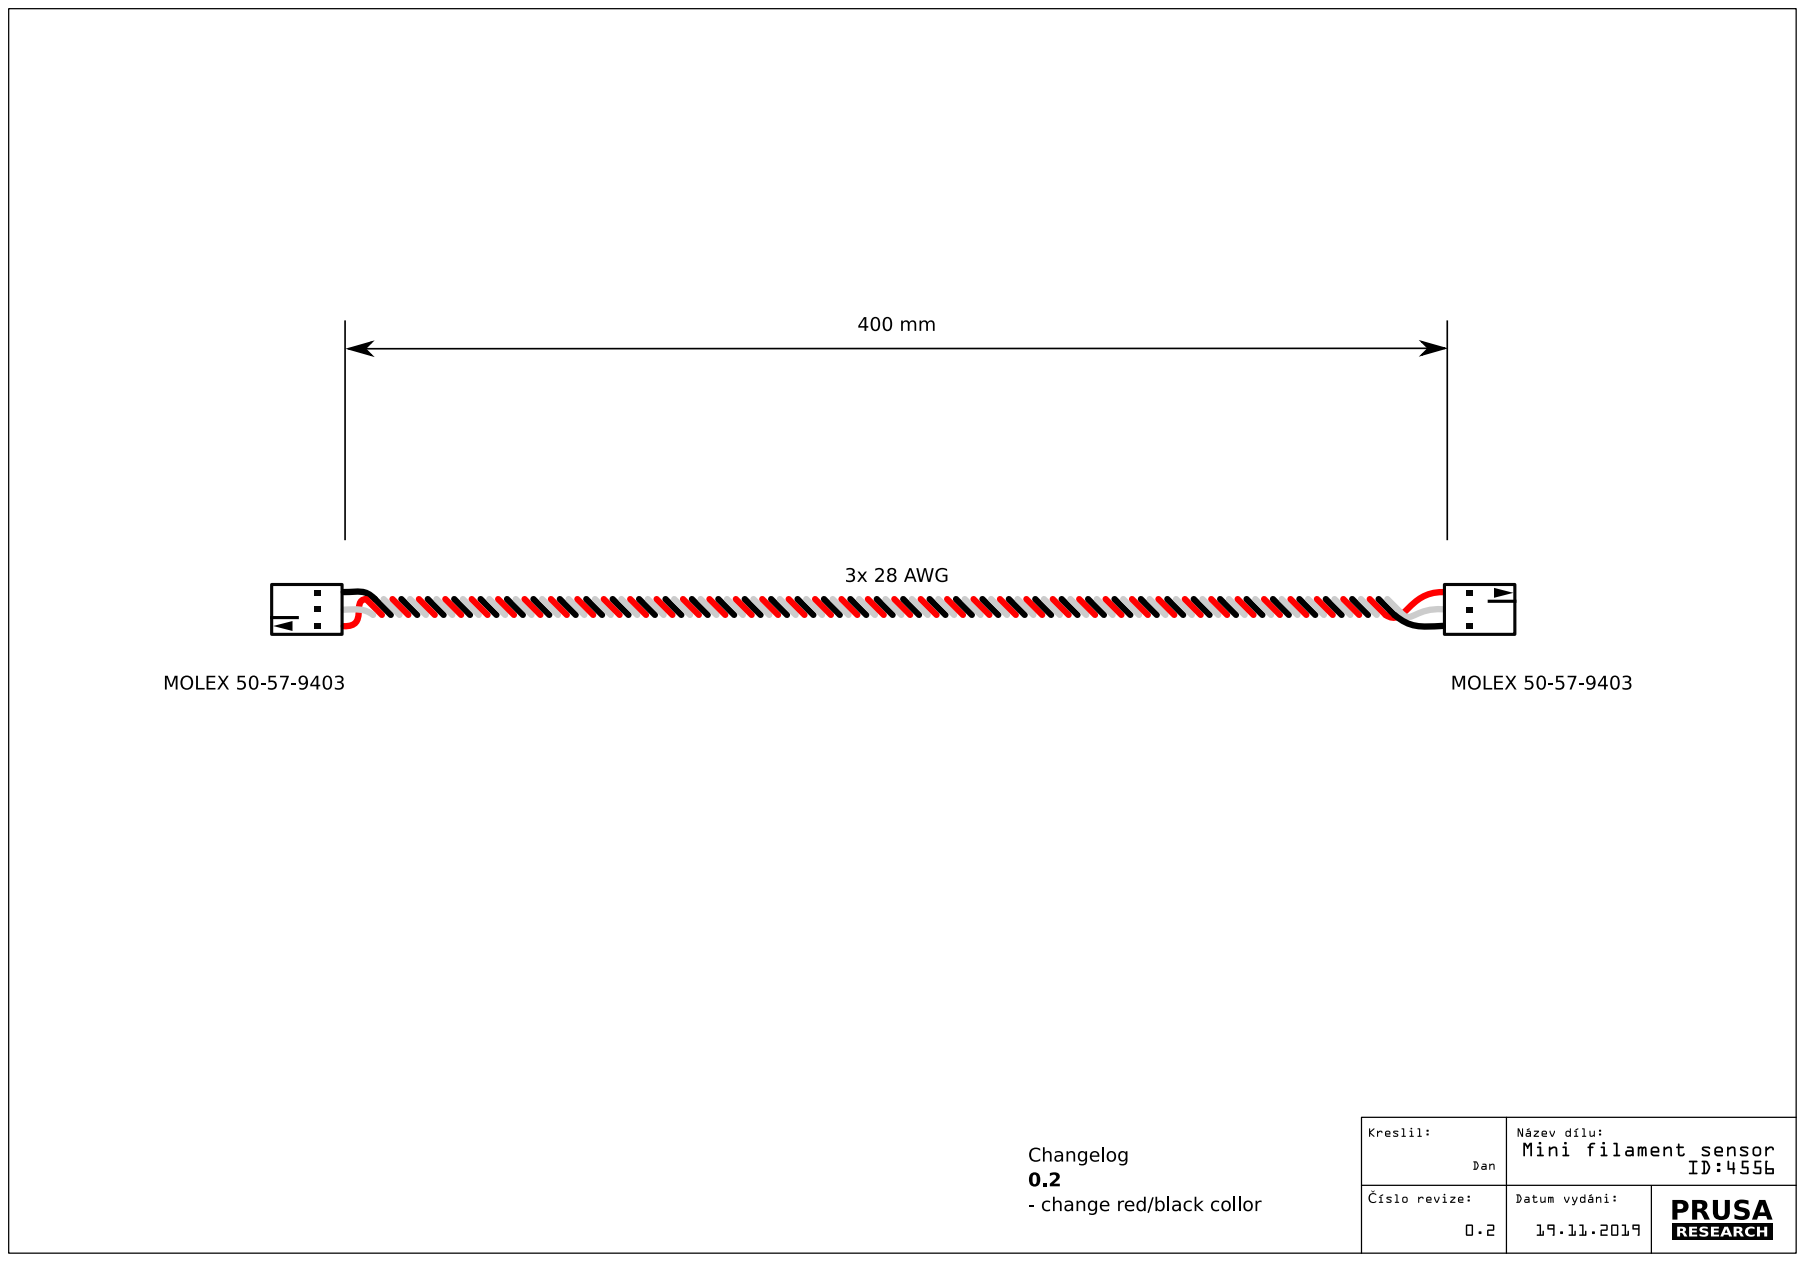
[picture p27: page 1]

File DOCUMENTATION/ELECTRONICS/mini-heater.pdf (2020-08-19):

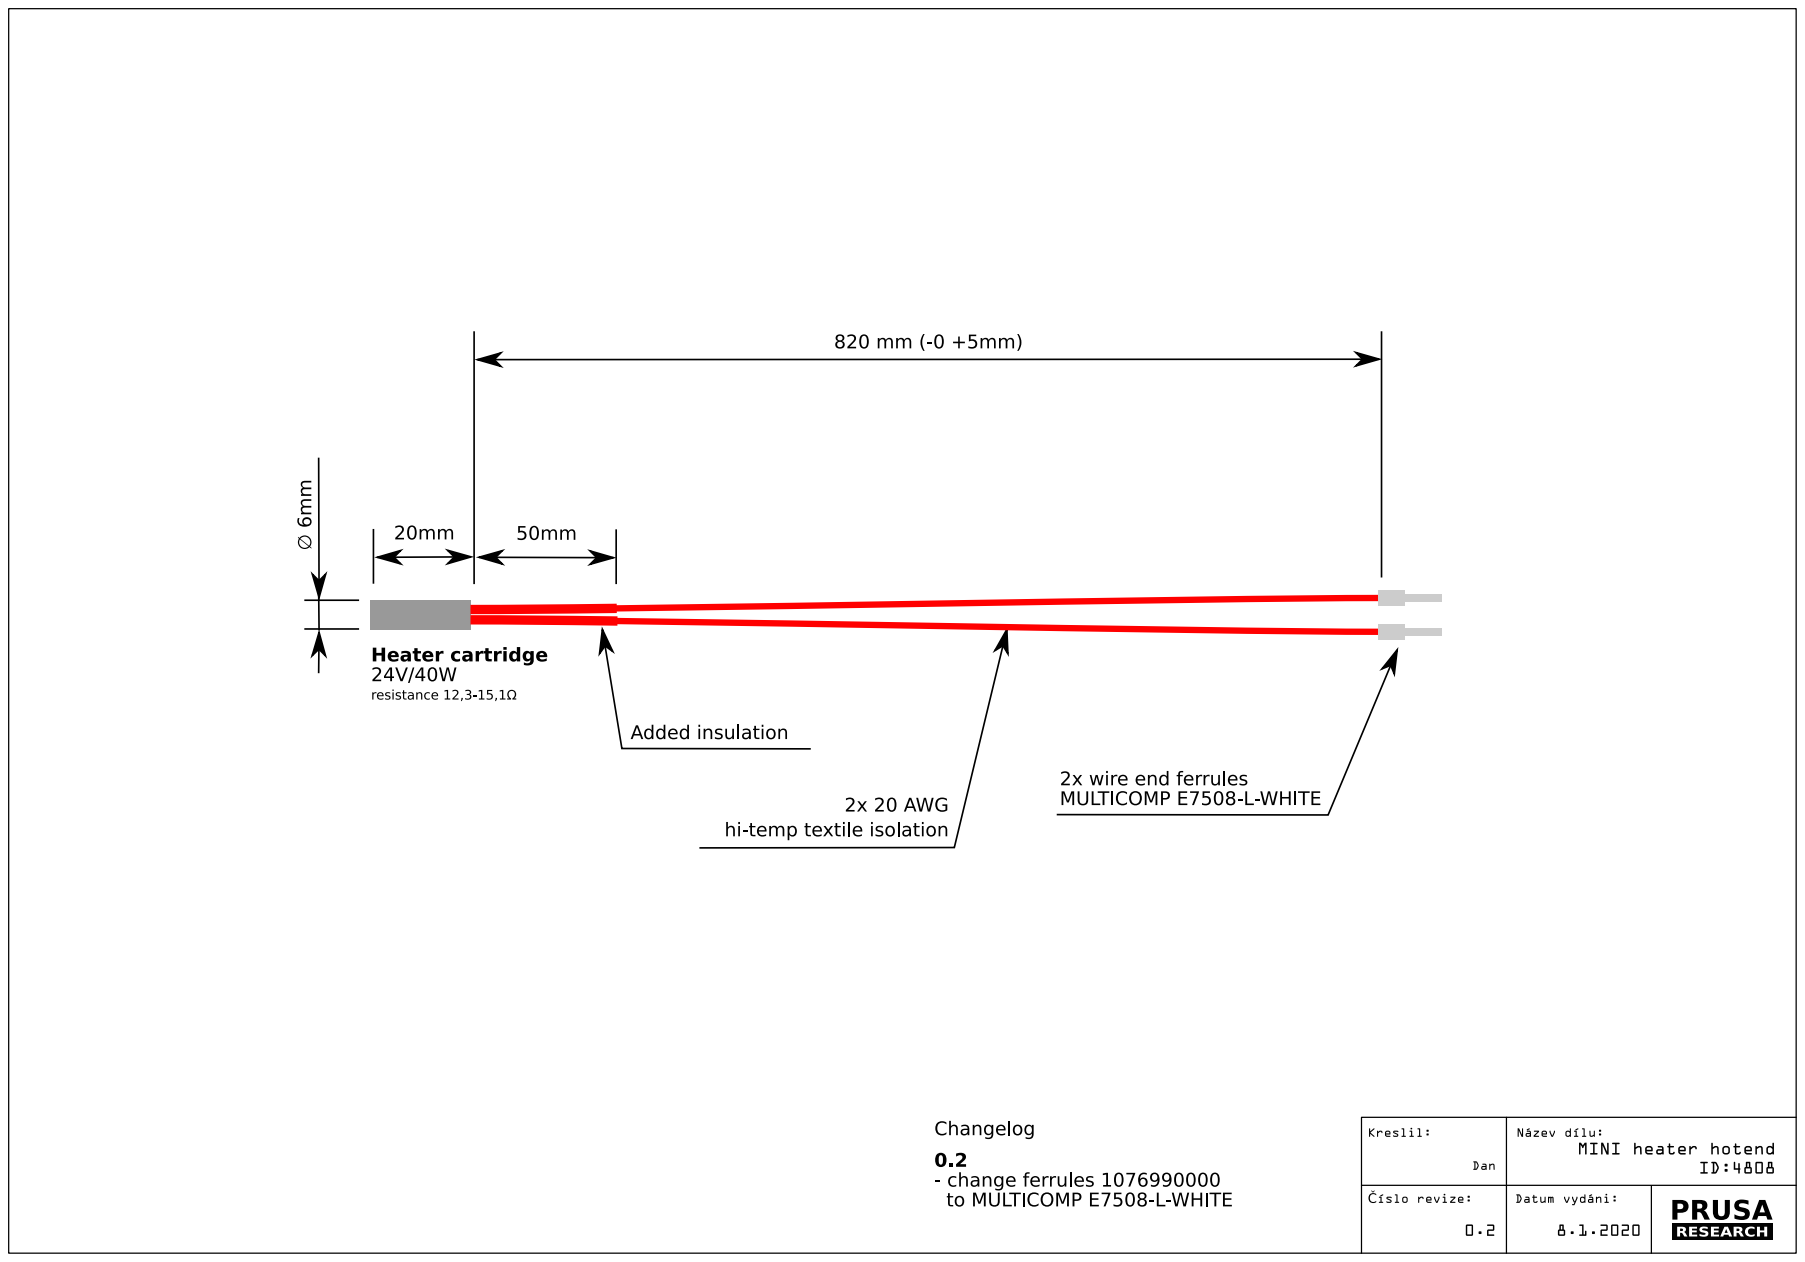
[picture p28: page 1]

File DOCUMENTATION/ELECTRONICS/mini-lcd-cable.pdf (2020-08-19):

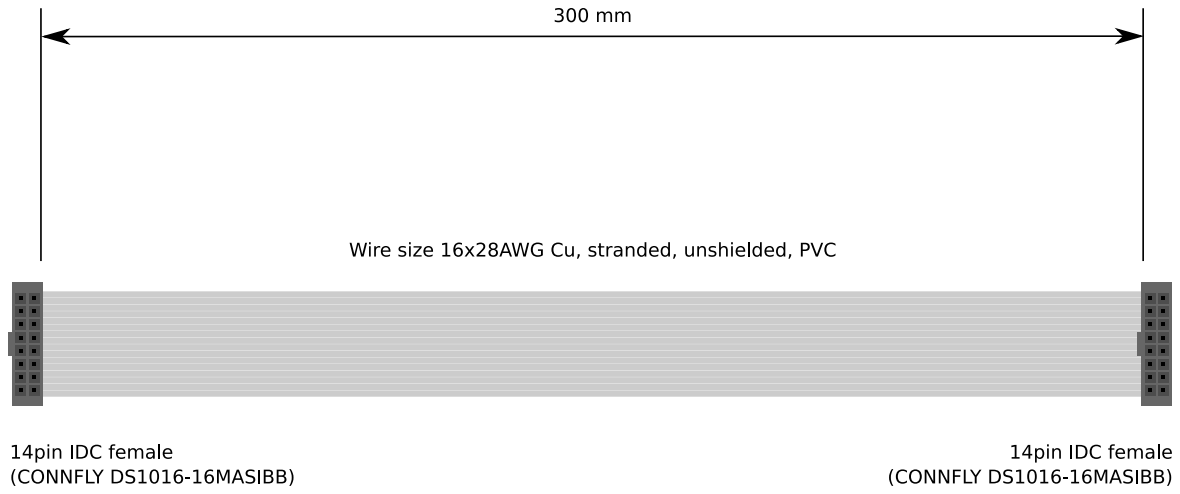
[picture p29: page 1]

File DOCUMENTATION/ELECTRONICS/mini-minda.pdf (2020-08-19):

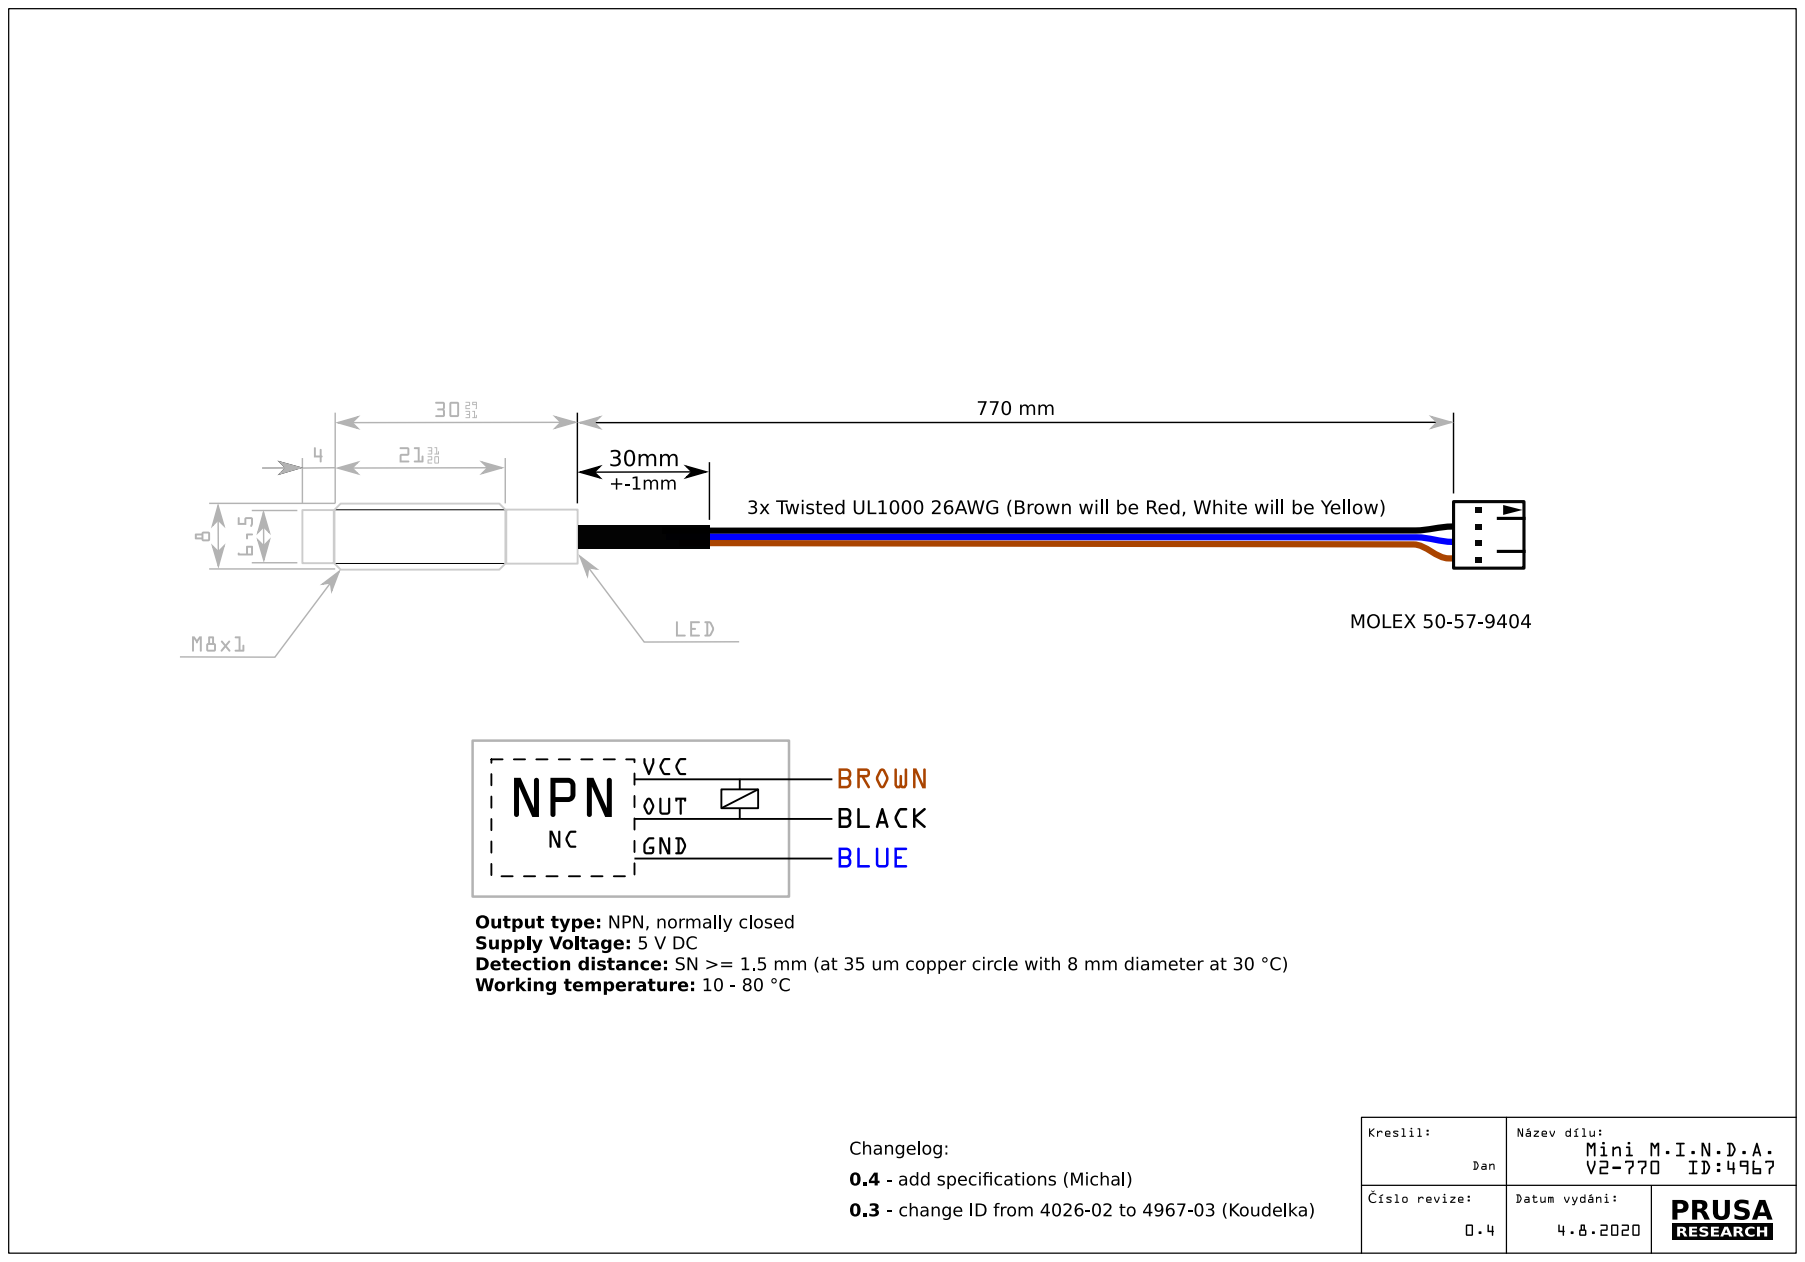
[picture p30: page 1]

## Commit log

2020-01-22 File renamed ( proper syntax )
    File renamed ( proper syntax )
    [MINI-inspection-door.stl]
2020-01-23 new mounting method of the extruder cables
    new mounting method of the extruder cables
    [MINI-fan-spacer-clip.stl, MINI-fan-spacer-clip.stp, MINI-fan-spacer.stl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]
2020-01-23 more robust part, held in place by 2 screws
    more robust part, held in place by 2 screws
    [MINI-minda-holder-clip.stl, MINI-minda-holder-clip.stp, MINI-minda-holder.stl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]
2020-01-23 belt slots adjusted
    belt slots adjusted
    [MINI-x-carriage.stl, MINI-x-carriage.stp]
2020-01-23 opening holes for screws holding part on the smooth rods
    opening holes for screws holding part on the smooth rods
    [MINI-x-end.stl, MINI-x-end.stp]
2020-01-23 increased height of the knob, deeper hole for encoder shaft
    - increased height of the knob
    - deeper hole for encoder shaft
    [MINI-knob.stl, MINI-knob.stp]
2020-01-23 screws adjusted, slots and cable management
    - adjusted screws holding Buddy board in place
    - reinforced slots for z-bottom-cover
    - opening for power connector adjusted for better printing
    - better aligment of USB connectors holes
    - slot for nut holding cover in place adjusted to eliminate nut falling from the slot
    [MINI-z-bottom.stp]
2020-01-23 wider protrusion for better cable management
    wider protrusion for better cable management
    [MINI-z-bottom-cover.stp]
2020-01-23 larger hole for encoder
    larger hole for encoder
    [MINI-display-box.stl, MINI-display-box.stp]
2020-01-23 missing part added
    missing part added
    [MINI-z-carriage-rear.stl]
2020-03-03 Heatbed thermistor cable space adjusted
    Heatbed thermistor cable space adjusted
    [MINI-heatbed-cable-cover-bottom.stl, MINI-heatbed-cable-cover-bottom.stp]
2020-03-03 Selective infill adjustment
    Selective infill adjustment
    [MINI-z-carriage-front.stl, MINI-z-carriage-front.stp]
2020-03-03 Selective infill adjustment , heatbed thermistor cable space adjusted
    Selective infill adjustment , heatbed thermistor cable space adjusted
    [MINI-heatbed-cable-cover-bottom.stp, MINI-z-carriage-front.stp]
2020-04-27 selective infill adjusted
    selective infill adjusted to start from bottom layers
    [MINI-extruder-idler.stl, MINI-extruder-idler.stp]
2020-04-27 larger hole for PTFE connector
    larger hole for PTFE connector
    [MINI-extruder-rear.stl, MINI-extruder-rear.stp]
2020-04-27 hole adjustments, selective infill
    - larger holes for z-plate
    - selective infill near walls as reinforcement middle M3S nut
    - deeper holes for hold-together screws ( M3x20 and M3x40 ) for better assembly
    [MINI-z-bottom.stl, MINI-z-bottom.stp]
2020-04-27 Selective infill, smooth rods seating adjusted
    - adjustment of selective infill
    - blind holes for smooth rods
    - slot for smooth rod adjusted and decreased width by 0.05mm
    [MINI-z-carriage-front.stl, MINI-z-carriage-front.stp]
2020-06-05 Missing parts added
    [MINI-filament-spur.stp, MINI-pinion.stp]
2020-08-19 Documentation, BOM and source code
    Documentation, BOM and source code
    [MINI-base-spoolholder.ipt, MINI-display-box.ipt, MINI-extruder-front.ipt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]
2020-08-21 Adjustments to avoid print problems
    Y-BELT_HOLDER : Length increased by 0.5 mm on both sides near channel for the wrench - thin wall elimination
    Y-IDLER : Chamfer near cut for the rib - thin wall elimination
    [MINI-y-belt-holder.ipt, MINI-y-belt-holder.stl, MINI-y-belt-holder.stp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]
2020-12-08 R7 and MINI+
    R7 and MINI+
    [MINI-bearing-clip.ipt, MINI-bearing-clip.stp, MINI-y-belt-holder.ipt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]
2021-02-07 MINI+ kit updates
    MINI+ kit version updates for easier assembly
    [MINI-display-box.ipt, MINI-display-box.stp, MINI-x-end.ipt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]
2021-02-14 Update README.md
    Updated link to assembly manual, MINI+ name updated
